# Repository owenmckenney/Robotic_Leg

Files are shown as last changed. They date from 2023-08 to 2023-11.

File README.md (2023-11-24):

 # 2 DOF Robotic Leg
Python code and CAD files for a single robotic leg. This design uses 2 [3D printed robotic actuators](https://github.com/owenmckenney/Robotic_Actuator) as well as a Raspberry Pi and mjbots pi3hat r4.5 to achieve planar leg motion. This leg mainly serves as a way to test the design of these actuators; another DOF oriented orthagonal to the current axis of rotation of the actuators would be necessary for a more functional and realistic leg as this would allow for easier turning during walking and would add a significant amount of stability to a full quadruped. The materials needed to replicate this design are listed in the [BOM](BOM.md). 

[CAD Overview](https://youtu.be/-uwau5FXpTE?si=GULFIlkYwvTJMZq1)

## Media

## Specs

- Thigh joint to knee joint: 200mm
- Knee joint to center of foot: 185mm
- 

## Manufacturing and Assembly 

- Most components fit together intuitively as there is only one way that this leg can be assembled. Only STL files are provided. For access to specifc source files, email owen.mckenney1@gmail.com.
- Larger prints may need to be oriented diagonally across the printbed depending on the kind of 3D printer being used.
- The 3D printed components of the original implementation were printed on a Ender 3 using PLA. All components have a naturally built-in tolerance of 0.2mm; this value may not be perfect depending on the tuning of your printer.
- Use of large width brims when slicing larger prints could be useful to prevent any warping during printing
- Pulleys should likely be printed with no support material; the addition of support can alter the shape of the pulley teeth and lead to belt slippage and skippage. The belt tensioner must also be implented for the same reasons.
- 

## Setup

Ensure all libraries and dependencies are installed, following the [moteus documentation](https://github.com/mjbots/moteus/tree/main). 

Follow proper construction and setup processes for the [robotic actuators](https://github.com/owenmckenney/Robotic_Actuator).

Set the correct servo ids for both the knee and thigh actuators, which are 2 and 1, respectively. Connect only the thigh actuator to JC1 on the pi3hat and use `sudo python3 -m moteus.moteus_tool -t 1 -c` to enter console and set the `id.id` to 1 using `conf set id.id 1`. Once this is set, the knee actuator can be daisychained and its `id.id` can be set to 2. 

Zero positions should be set for both the knee and calf joints using `sudo python3 -m moteus.moteus_tool --target 1 --zero-offset` and `sudo python3 -m moteus.moteus_tool --target 2 --zero-offset` while the leg is oriented in a completed downward position (thigh and calf are colinear and pointed down). 

Set `servopos.position_min` and `servopos.position_max` to `-3.0`, `0.5` and `-3.2`, `0.5` for the thigh and knee servo, respectively. Without these limits set, the leg is susceptible to major failure as the joints may try to move to positions not physically allowed. 

Reference the moteus documentation for additional guidance on how to set up the pi3hat, configure the actuator ids, and set position limits.

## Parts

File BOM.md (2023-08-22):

# Bill of Materials

- 3D Printed robotic actuator (2x) - [link](https://github.com/owenmckenney/Robotic_Actuator/tree/main)
- 17x23x4mm bearing - [link](https://www.amazon.com/gp/product/B082PRVKPR/ref=ppx_yo_dt_b_search_asin_title?ie=UTF8&psc=1)
- M3 threaded inserts - [link](https://www.amazon.com/dp/B087NBYF65?psc=1&ref=ppx_yo2ov_dt_b_product_details)
- 180T x 9mm Wide Timing Belt (GT2 3mm) - [link](https://www.vexrobotics.com/gt2-timingbelts.html)
- 8mm M3 socket head cap screws (4x)
- 12mm M3 socket head cap screws (10x)
- 16mm M3 socket head cap screws (4x)
- 35mm M3 socket head cap screws (4x)

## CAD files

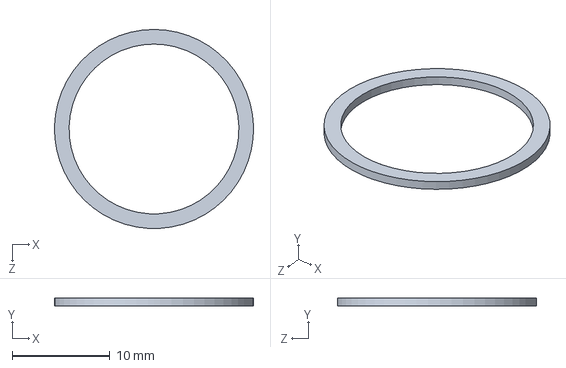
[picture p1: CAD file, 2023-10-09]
hardware/Knee Joint Spacer.SLDPRT
20.4 x 0.8 x 20.4 mm

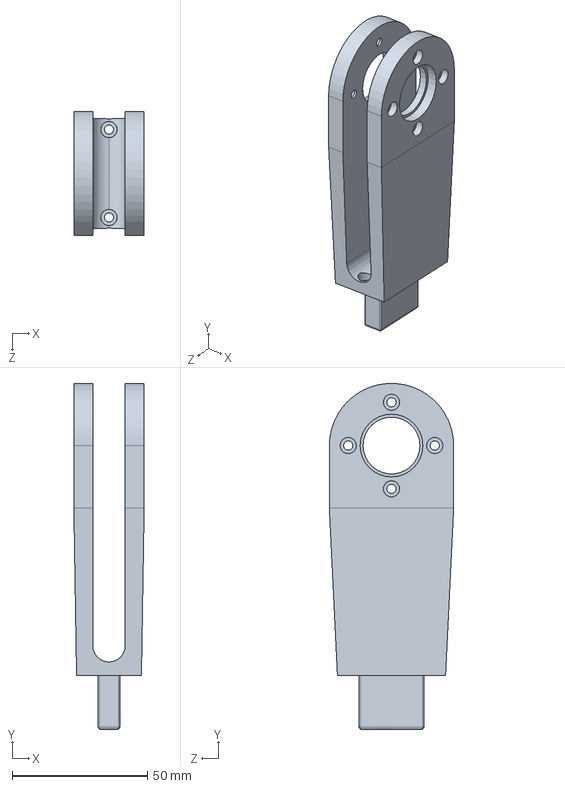
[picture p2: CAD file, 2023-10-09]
hardware/Calf Joint.SLDPRT
26.0 x 127.9 x 46.0 mm

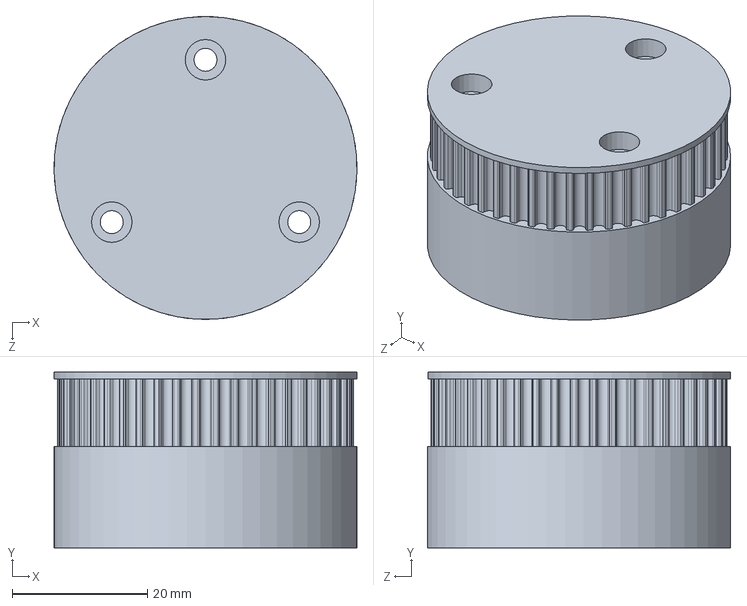
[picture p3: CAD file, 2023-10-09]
hardware/Pulley.SLDPRT
44.8 x 26.0 x 44.8 mm

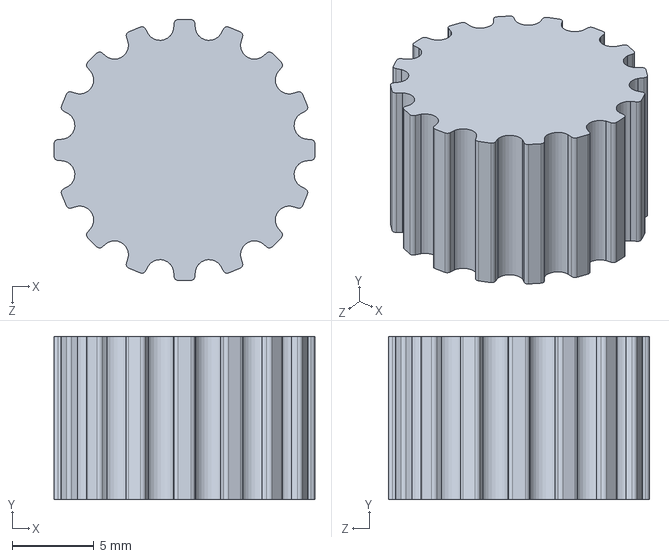
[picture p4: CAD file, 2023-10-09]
hardware/Actuator Pulley.SLDPRT
16.0 x 10.0 x 16.0 mm

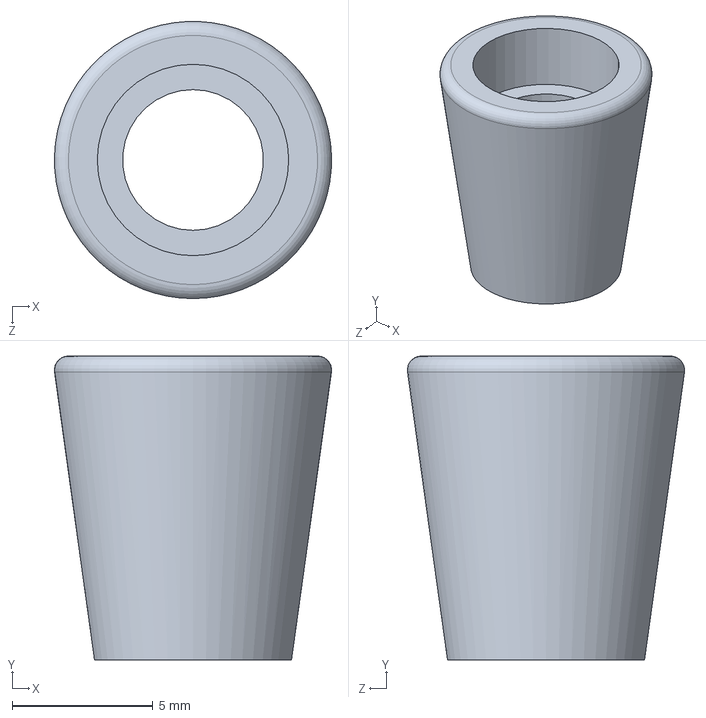
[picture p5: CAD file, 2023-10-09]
hardware/Tension Spacer.SLDPRT
9.84 x 10.8 x 9.84 mm

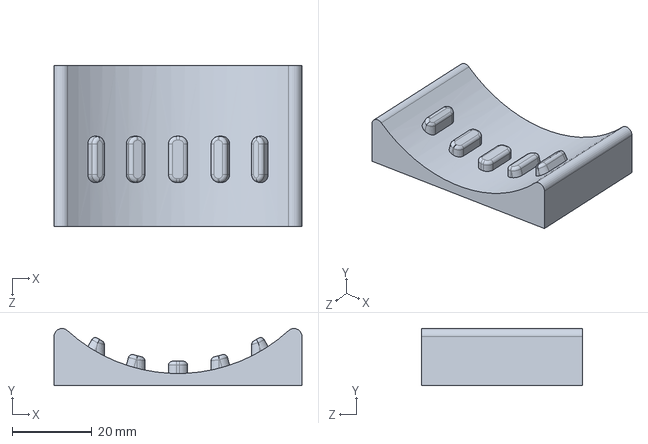
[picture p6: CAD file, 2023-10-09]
hardware/Squarer.SLDPRT
62.0 x 14.3 x 40.3 mm

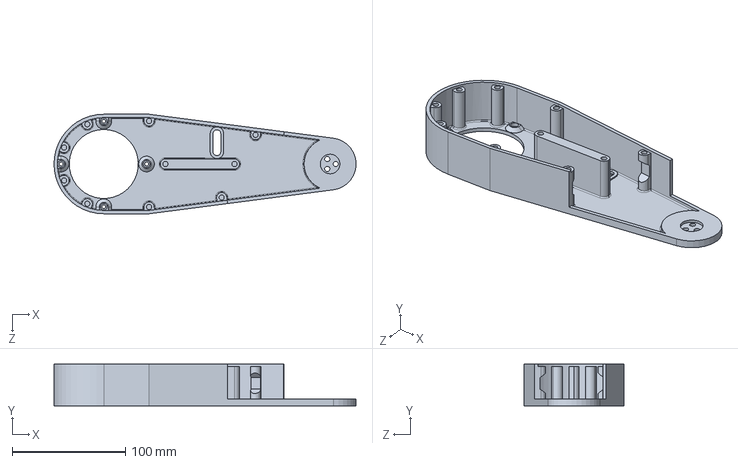
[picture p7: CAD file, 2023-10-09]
hardware/Leg.SLDPRT
266.9 x 37.0 x 88.0 mm

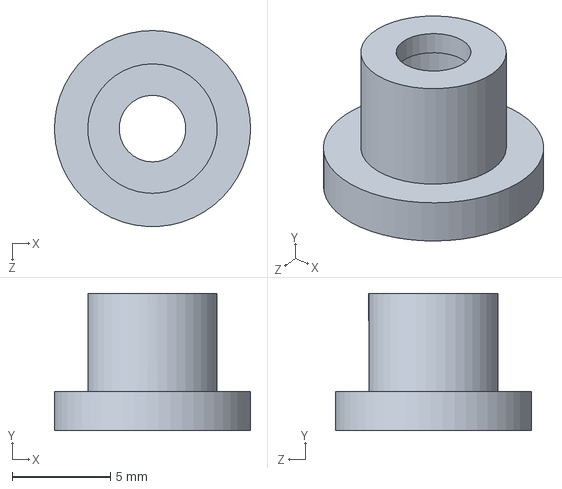
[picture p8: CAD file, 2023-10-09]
hardware/Tension Rod Cap.SLDPRT
10.00 x 7.00 x 9.99 mm

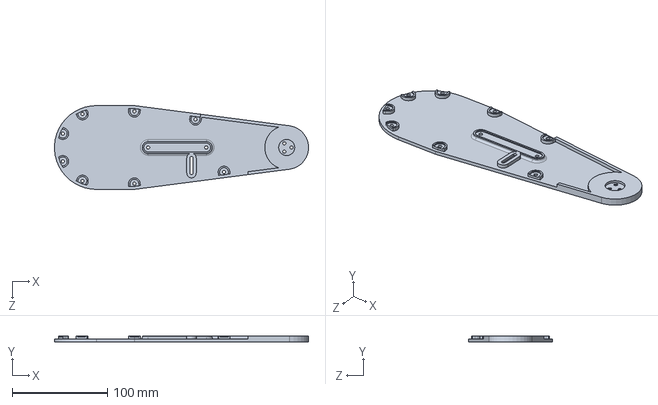
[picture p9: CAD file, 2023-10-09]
hardware/Leg Lid.SLDPRT
266.8 x 6.00 x 88.0 mm

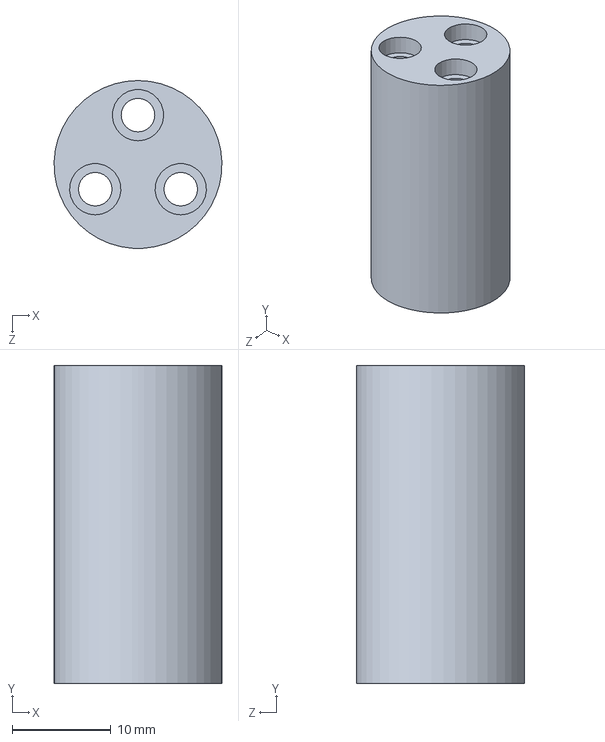
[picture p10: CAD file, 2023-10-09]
hardware/Knee Joint Rod.SLDPRT
17.0 x 32.2 x 17.0 mm

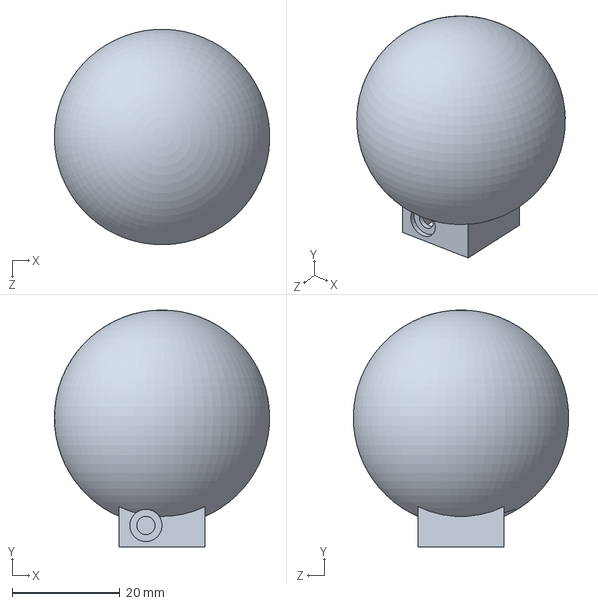
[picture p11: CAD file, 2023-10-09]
hardware/Foot.SLDPRT
40.0 x 44.0 x 40.0 mm

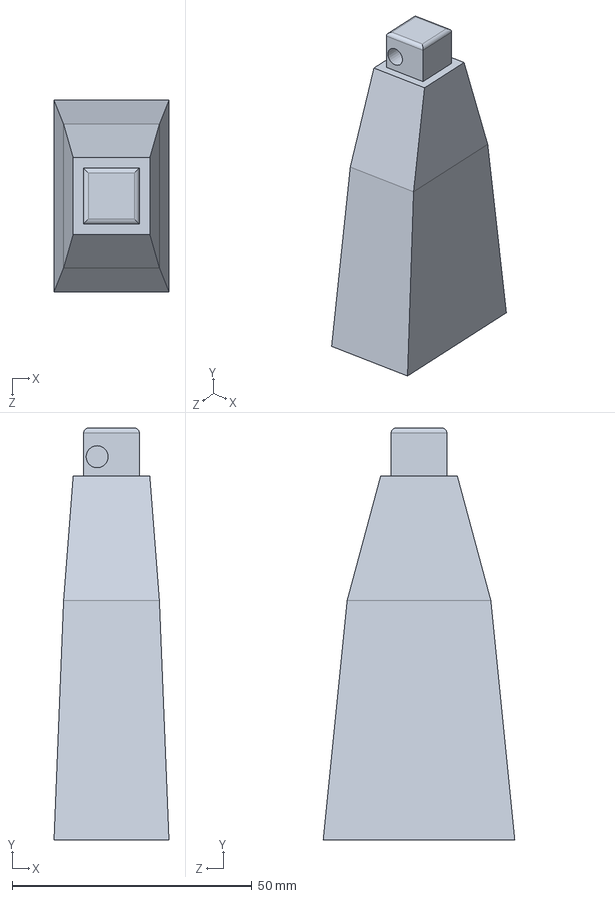
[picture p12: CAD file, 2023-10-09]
hardware/Calf.SLDPRT
24.0 x 86.0 x 40.0 mm

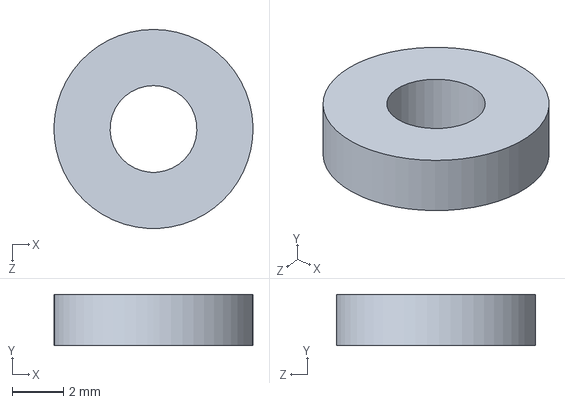
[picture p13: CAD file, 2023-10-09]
hardware/Washer.SLDPRT
7.80 x 2.00 x 7.80 mm

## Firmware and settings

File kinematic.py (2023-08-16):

# commands foot to x/y coordinate based on x/y input
# calculates angles for thigh and knee, converts to positional values

import math
import time
import asyncio
import argparse
import moteus
import moteus_pi3hat
import sys

a = 200
b = 185

transport = moteus_pi3hat.Pi3HatRouter(
    servo_bus_map = {
        1:[11],
        2:[11]
    }
)

hip_servo = moteus.Controller(id=1, transport=transport)
knee_servo = moteus.Controller(id=2, transport=transport)

async def zero():
    commands = [
        hip_servo.make_position(
            position = 0,
            accel_limit = 2.0, 
            velocity_limit = 4.0,
            maximum_torque = 0.15, 
            watchdog_timeout = math.nan
            ),
        knee_servo.make_position(
            position = 0,
            accel_limit = 2.0,
            velocity_limit = 4.0,
            maximum_torque = 0.15,
            watchdog_timeout = math.nan
        )
    ]
    
    results = await transport.cycle(commands)

def calculate_positions(a, b, x, y, hip_pos, knee_pos):
    gamma = math.atan(x/y)
    theta = math.acos(((x**2 + y**2) + a**2 - b**2)/(2*a*math.sqrt(x**2 + y**2)))
    phi = math.acos((a**2 + b**2 - x**2 - y **2)/(2*a*b))

    previous_hip_pos = hip_pos
    previous_knee_pos = knee_pos

    hip_pos = math.degrees(theta + gamma) * 1/360 * -8 
    knee_pos = (180 - math.degrees(phi)) * 1/360 * 8

    return hip_pos, knee_pos, previous_hip_pos, previous_knee_pos


def calculate_velocities(hip_pos, knee_pos, previous_hip_pos, previous_knee_pos, vel_high, accel):
    hip_pos_diff = abs(hip_pos - previous_hip_pos)
    knee_pos_diff = abs(knee_pos - previous_knee_pos)

    #print("Hip pos diff: ", hip_pos_diff, "Knee pos diff: ", knee_pos_diff)

    t = round((-vel_high + math.sqrt(vel_high**2 - 4*(accel/2)*-max(hip_pos_diff, knee_pos_diff)))/(2*(accel/2)), 4)
    vel_low = (min(hip_pos_diff, knee_pos_diff) - accel/2 * t**2)/t

    #print("t: ", t, "vel low: ", vel_low)

    if hip_pos_diff > knee_pos_diff:
        hip_vel = vel_high
        knee_vel = vel_low
    elif hip_pos_diff < knee_pos_diff: 
        hip_vel = vel_low
        knee_vel = vel_high
    else:
        hip_vel = vel_high
        knee_vel = vel_high

    return hip_vel, knee_vel

async def move(hip_pos, knee_pos, hip_vel, knee_vel, accel):
    
    commands = [
        hip_servo.make_position(
            position = hip_pos,
            accel_limit = accel, 
            velocity_limit = hip_vel,
            maximum_torque = 0.15, 
            watchdog_timeout = math.nan,
            query = True
        ),
        knee_servo.make_position(
            position = knee_pos,
            accel_limit = accel,
            velocity_limit = knee_vel,
            maximum_torque = 0.15,
            watchdog_timeout = math.nan,
            query = True
        )
    ]

    results = await transport.cycle(commands)

async def main():

    await hip_servo.set_stop()
    await knee_servo.set_stop()
    await zero()

    mode = int(input("1 for coordinate controlled movement, 2 for walking sequence: "))
    
    if mode == 1:
        hip_pos = 0
        knee_pos = 0
        vel_high = 16.0
        accel = 8.0

        try:
            while True:
                y = round(float(input("enter desired y displacement: ")), 4)
                x = round(float(input("enter desired x displacement: ")), 4)

                positions = calculate_positions(a, b, x, y, hip_pos, knee_pos)
                hip_pos = positions[0]
                knee_pos = positions[1]

                print("Hip pos: ", hip_pos, "Knee pos: ", knee_pos)

                velocities = calculate_velocities(hip_pos, knee_pos, positions[2], positions[3], vel_high, accel)
                hip_vel = velocities[0]
                knee_vel = velocities[1]

                print("hip vel: ", hip_vel, "knee vel: ", knee_vel)

                await move(hip_pos, knee_pos, hip_vel, knee_vel, accel)

        except KeyboardInterrupt:
            await hip_servo.set_stop()
            await knee_servo.set_stop()
            sys.exit("interrupt")

    
    elif mode == 2:
        time.sleep(1)

        hip_pos = 0
        knee_pos = 0

        try:
            while True:
                x = -100
                y = 250

                initial_pos = calculate_positions(a, b, x, y, hip_pos, knee_pos)
                velocities = calculate_velocities(initial_pos[0], initial_pos[1], initial_pos[2], initial_pos[3], 16.0, 8.0)
                await move(initial_pos[0], initial_pos[1], velocities[0], velocities[1], 8.0)

                time.sleep(1)

                for x in range(-100, 201):
                    y = 250
                    positions = calculate_positions(a, b, x, y, hip_pos, knee_pos)
                    
                    await move(positions[0], positions[1], 10.0, 10.0, 8.0)

                c = 100
                d = 50
                k = 200

                for x in range(200, -99):                    
                    y = (d*math.sqrt(c**2 - x**2))/c + k
                    positions = calculate_positions(a, b, x, y, hip_pos, knee_pos)

        except KeyboardInterrupt:
            await hip_servo.set_stop()
            await knee_servo.set_stop()
            sys.exit("interrupt")

    else:
        await hip_servo.set_stop()
        await knee_servo.set_stop()
        sys.exit("invalid input")
        
if __name__ == '__main__':
    asyncio.run(main())
